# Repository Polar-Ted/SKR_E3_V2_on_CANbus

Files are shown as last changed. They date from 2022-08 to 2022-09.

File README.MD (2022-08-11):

# SKR Mini E3 V2 on CANBUS

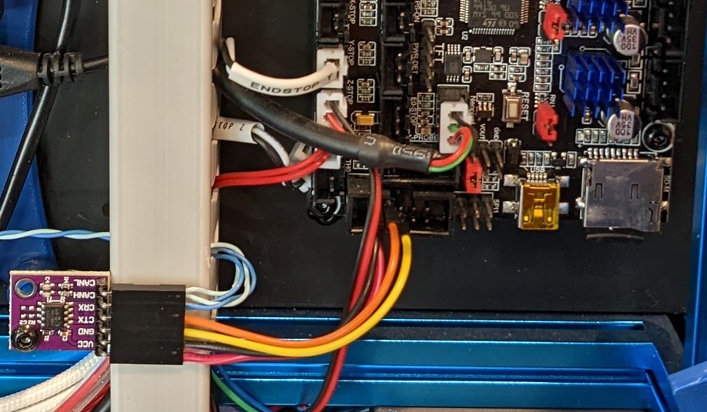
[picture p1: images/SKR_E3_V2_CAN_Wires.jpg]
Wiringimage
      

Wiring and config to run the SKR Mini E3 V2 over CAN

## Setup Steps

### Compile Toolboard Firmware
- ssh to your pi console
- CD to the klipper directory
```
cd klipper
```
- Run MAKE Clean
```
make clean
```
- open menuconfig
```
make menuconfig
```
- Set the following options for CANBUS connection  
    Note: If you already have a CAN implementation set the CANBUS speed to match your existing configuration. Common speeds are 250000 and 500000

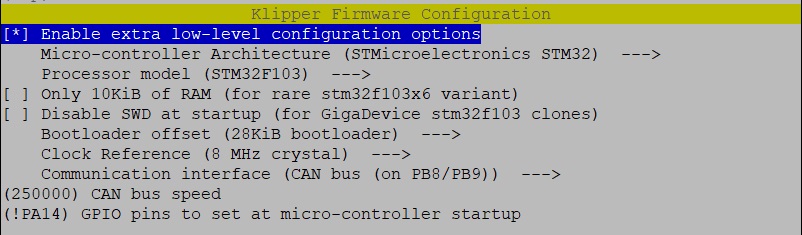
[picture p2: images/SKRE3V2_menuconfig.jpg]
Config


-Run make
```
make
```
-When the make is complete connect to the klipper host with SFTP and 
navigate to the Klipper out file
```
 /home/pi/klipper/out
```
- Copy the Klipper.bin file to your local machine 
- Rename the file to firmware.bin
- Transfer firmware.bin to your microSD card
- Replace the microSD card into the Mini E3.
- Power on the system. SKR will automatically update with the Klipper firmware.

## Wiring Diagram

    Note: The MCP2551 does not have 120 ohm resistors. If this is the only device on your CANBUS you will need to wire a 120 ohm resistor between CANH and CANL at the MCP2551 connector.  You CANBUS should measure 60 ohms between CAN H and CAN L with all the devices connected. ( measure while powered off) 

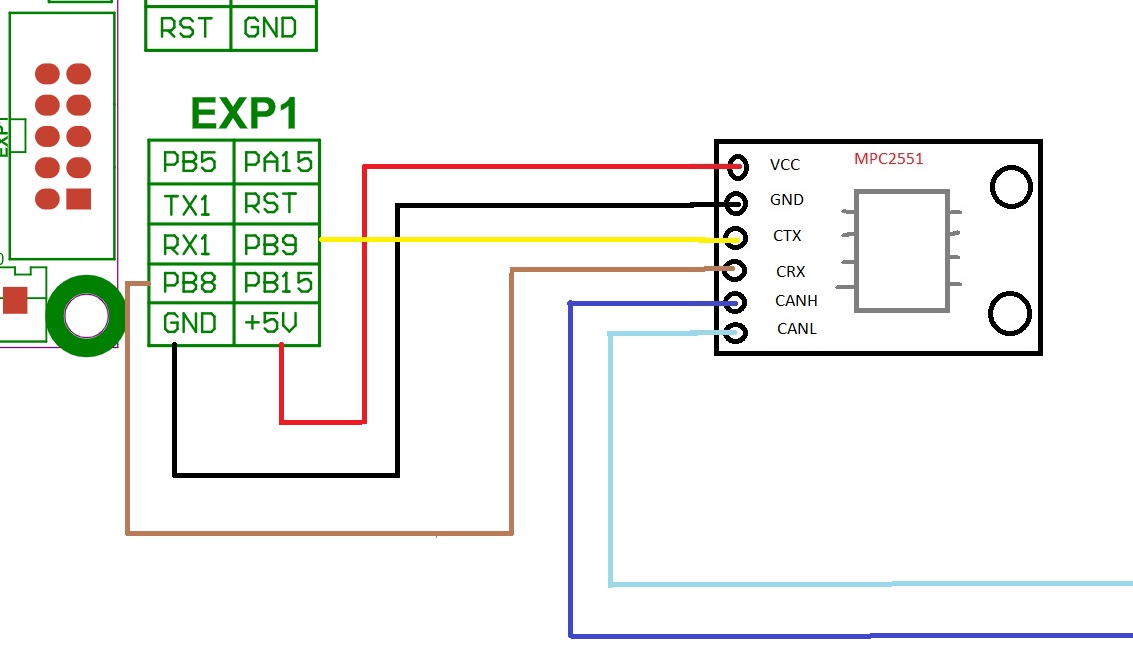
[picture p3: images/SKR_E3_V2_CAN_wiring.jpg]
Wiring
      

## Links  

  [MCP2551 board](https://www.aliexpress.com/item/2255800362518857.html?spm=a2g0o.order_list.0.0.21ef1802WJAiGd)
  
  [SKR Mini E3 V2](https://github.com/bigtreetech/BIGTREETECH-SKR-mini-E3/tree/master/hardware/BTT%20SKR%20MINI%20E3%20V2.0/Hardware)
  
  [Maz0r CanBus Configuratuion and troubleshooting guides](https://maz0r.github.io/klipper_canbus/)
  
  [rootiest guide to SKR Pico as a USB Can bridge](https://github.com/rootiest/zippy-klipper_config/blob/master/guides/Guide-pico_can.md)

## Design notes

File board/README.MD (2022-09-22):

## Project to create a plug in CAN board for the EXP1 socket on the SKR Mini E3 V2 and V3.        ##

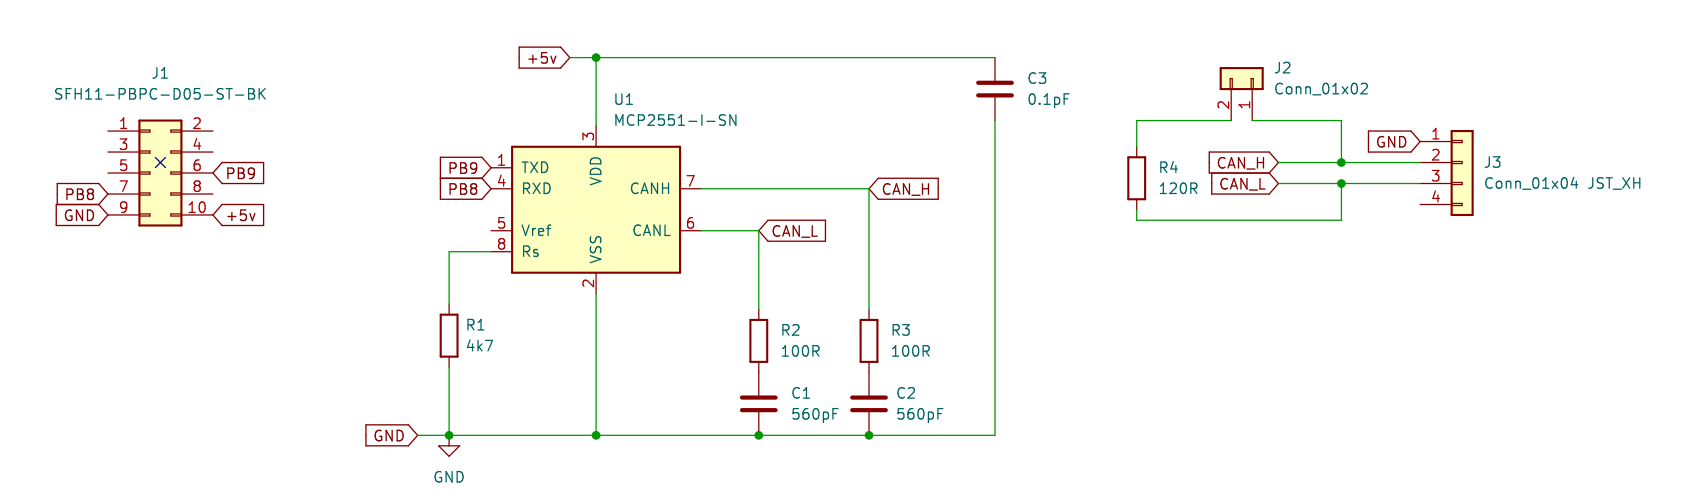
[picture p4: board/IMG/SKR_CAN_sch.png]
board schematic
      
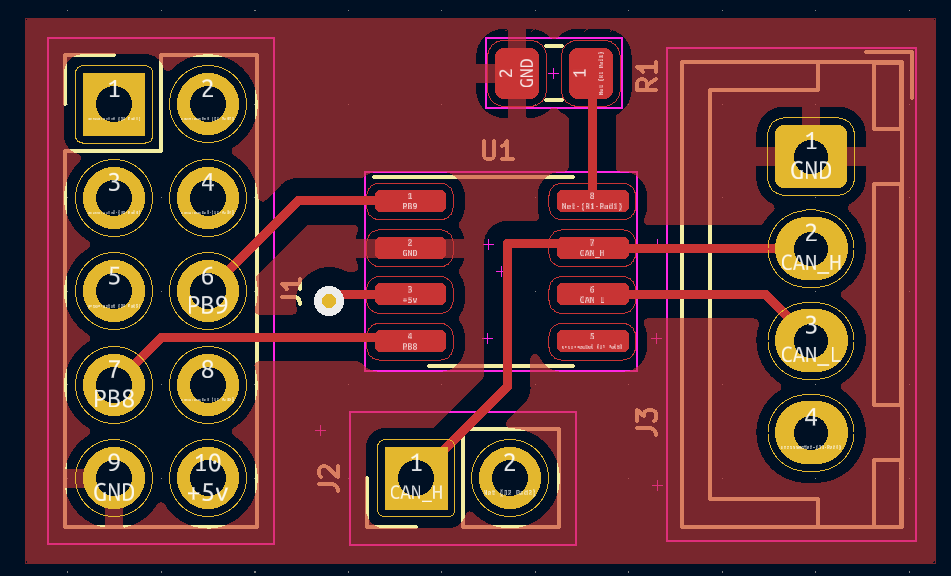
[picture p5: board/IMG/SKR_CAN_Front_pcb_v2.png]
      
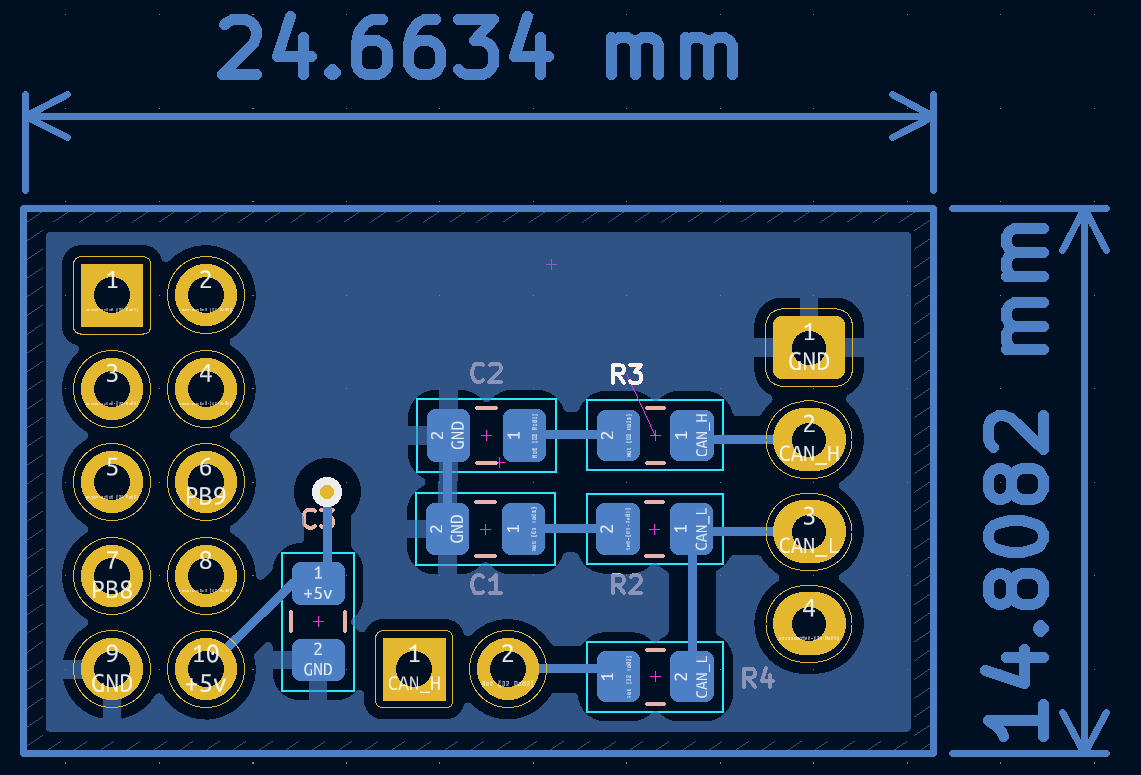
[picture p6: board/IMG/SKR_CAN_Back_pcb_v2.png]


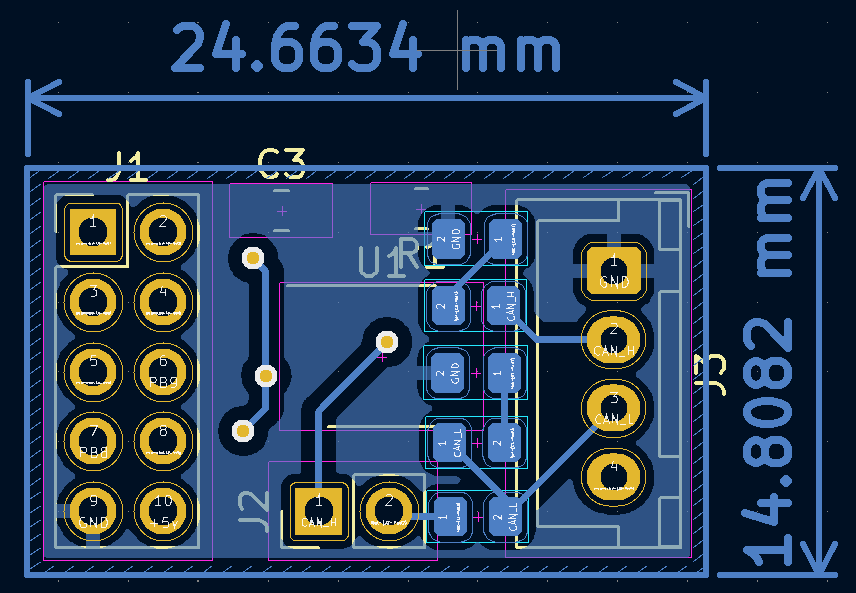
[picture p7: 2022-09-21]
board/IMG/SKR_CAN_Back_pcb.png

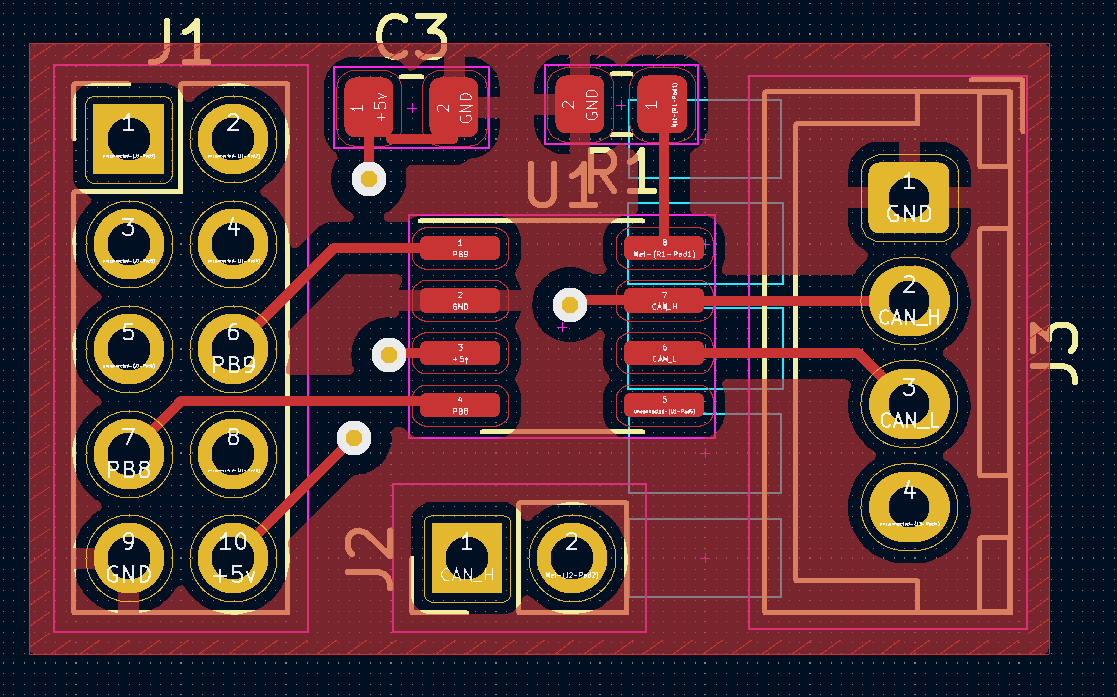
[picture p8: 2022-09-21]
board/IMG/SKR_CAN_Front_pcb.png

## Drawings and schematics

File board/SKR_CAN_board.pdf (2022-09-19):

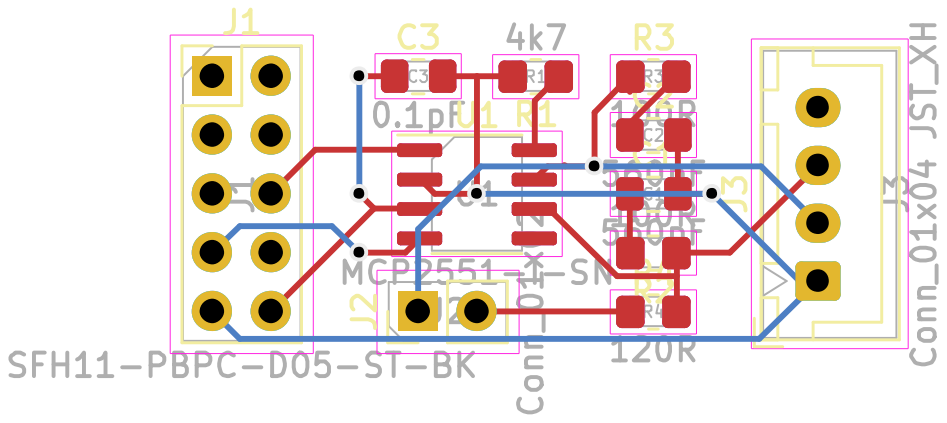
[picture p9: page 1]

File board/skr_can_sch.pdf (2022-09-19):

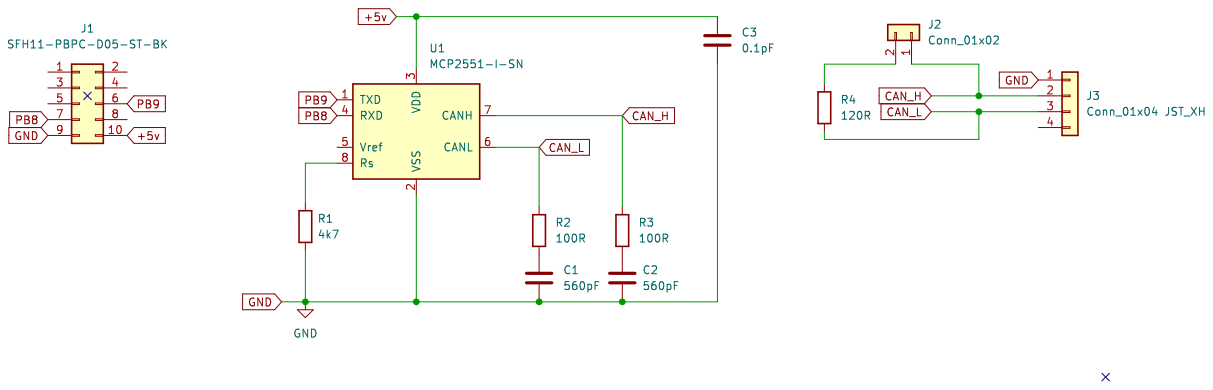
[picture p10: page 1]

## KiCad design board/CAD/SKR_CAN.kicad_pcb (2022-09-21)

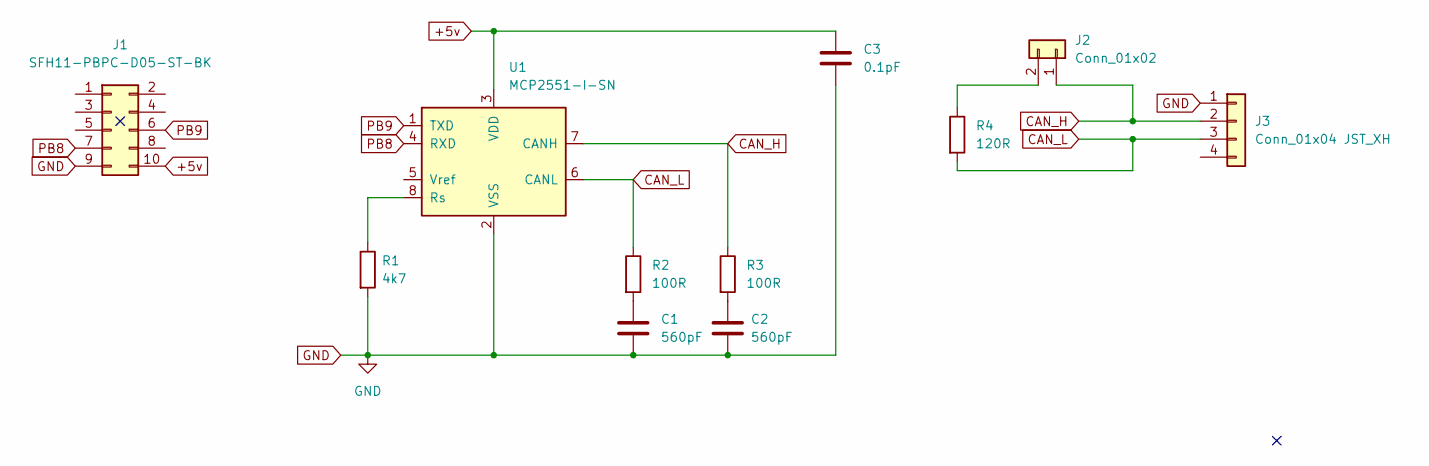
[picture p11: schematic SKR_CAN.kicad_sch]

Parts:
C1, C2: 560pF; C_0805_2012Metric_Pad1.18x1.45mm_HandSolder
C3: 0.1pF; C_0805_2012Metric_Pad1.18x1.45mm_HandSolder
J1: SFH11-PBPC-D05-ST-BK; PinHeader_2x05_P2.54mm_Vertical
J2: Conn_01x02; PinHeader_1x02_P2.54mm_Vertical
J3: Conn_01x04 JST_XH; JST_XH_B4B-XH-A_1x04_P2.50mm_Vertical
R1: 4k7; R_0805_2012Metric_Pad1.20x1.40mm_HandSolder
R2, R3: 100R; R_0805_2012Metric_Pad1.20x1.40mm_HandSolder
R4: 120R; R_0805_2012Metric_Pad1.20x1.40mm_HandSolder
U1: MCP2551-I-SN; SOIC-8_3.9x4.9mm_P1.27mm

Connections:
+5v: C3.1, J1.10, U1.3 (VDD)
CAN_H: J2.1, J3.2, R3.1, U1.7 (CANH)
CAN_L: J3.3, R2.1, R4.2, U1.6 (CANL)
GND: C1.2, C2.2, C3.2, J1.9, J3.1, R1.2, U1.2 (VSS)
unnamed: C1.1, R2.2
unnamed: C2.1, R3.2
unnamed: J2.2, R4.1
unnamed: R1.1, U1.8 (Rs)
PB8: J1.7, U1.4 (RXD)
PB9: J1.6, U1.1 (TXD)

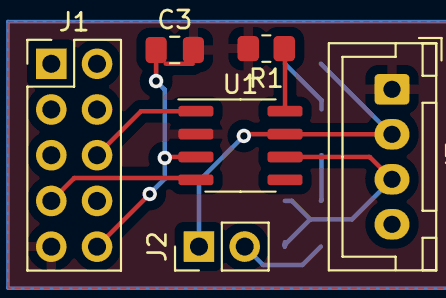
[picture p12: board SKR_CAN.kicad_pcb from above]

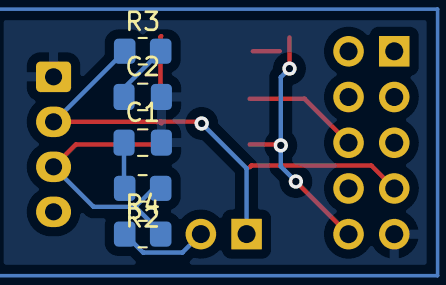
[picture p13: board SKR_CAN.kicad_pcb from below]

Board: 2 copper layers, 11 parts (5 on the bottom side), 10 nets.

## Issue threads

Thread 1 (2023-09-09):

Is there a way to verify the SKR is visible on the CAN network?

Fuergrissa1, 2023-09-09:
`python3 ~/katapult/scripts/flashtool.py -i can0 -q`

Shows me all of the nodes on the CAN network and their UUID but I don't see the SKR or the MCP2551 on the list, is this normal?

Do you have any information on how to find the UUID to list in the klipper config for the MCU?

Fuergrissa1, 2023-09-10:
I had made a mistake, compiled firmware for F103, but my SKR mini e3 V3 uses a G0B1, re flashed with new firmware and the UUID does show on the list. Thank you!

Closed 2023-09-10.
